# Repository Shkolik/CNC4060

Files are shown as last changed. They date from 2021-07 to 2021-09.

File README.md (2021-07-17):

# DIY CNC router with work area around 400x600mm 

Hi everyone! It's my first attempt to model CNC router in CAD software. Work still in progress, but CAD pretty much done. 

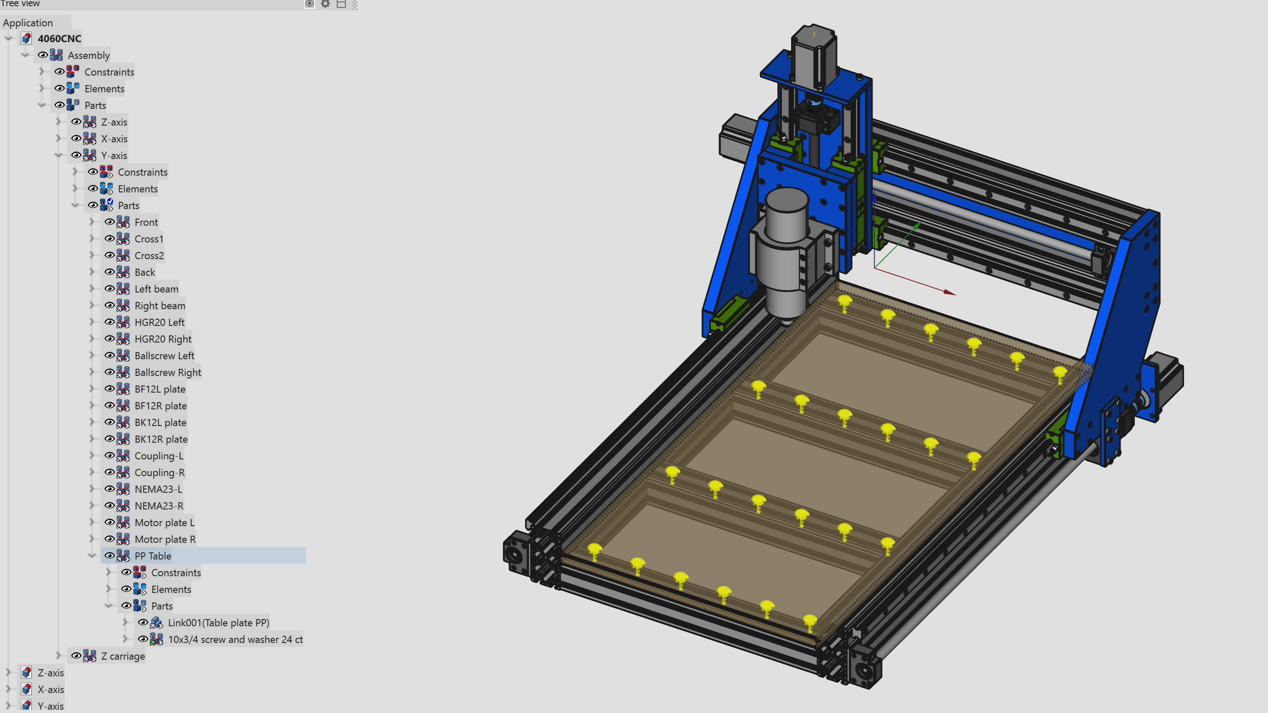
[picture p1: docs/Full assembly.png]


# Materials

Router made of 10 series fractional aluminum extrusion profiles and aluminum flat stock. Base made of 2 2"x4" side profiles and 4 2"x2" cross members. Gantry made of 2 2"x2" profiles that tied together with 1/2" aluminum plate. All sizes and shapes made to fit widely available flat stock.

Fasteners are mix of metric and imperial threads just because all linear motion hardware use metric, but fractional extrusion wants imperial. You can use all metric, but it will require some additional work.

# CAD

Project created in FreeCAD Link. You can find latest releases here: https://github.com/realthunder/FreeCAD_assembly3/releases

Also you need to install Fasteners workbench: https://github.com/shaise/FreeCAD_FastenersWB

To open project without errors and broken links please maintain folders structure as-is.

## Disclaimer

This project provided as-is. You can use it to create you own CNC, but there is no guarantee that it will work as you want and will not produce any loss or injury. 
**Work still in progress!** 

If you have any suggestions - post them as issue inside this repo.

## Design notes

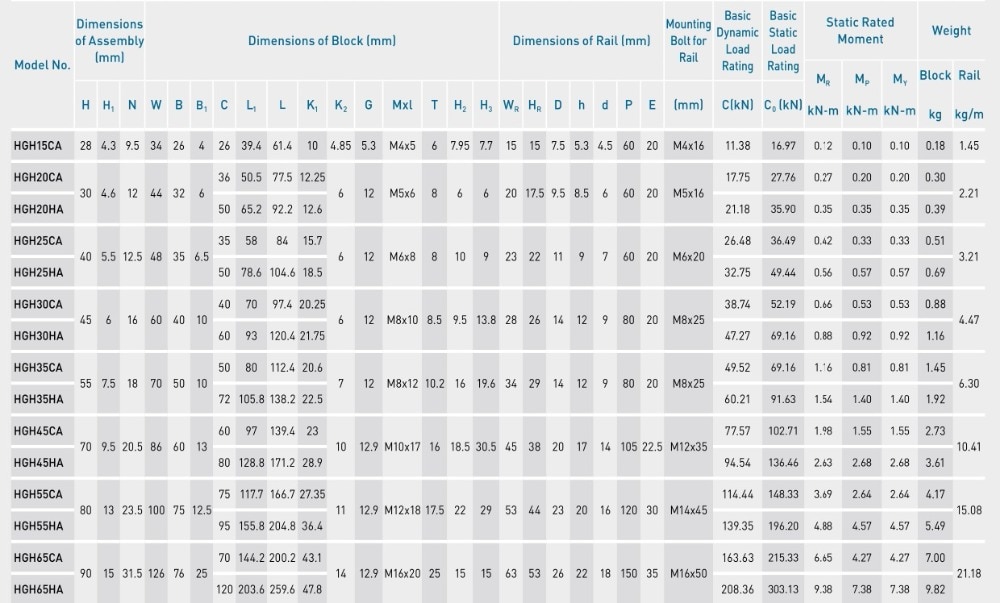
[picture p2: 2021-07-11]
docs/rails.jpg

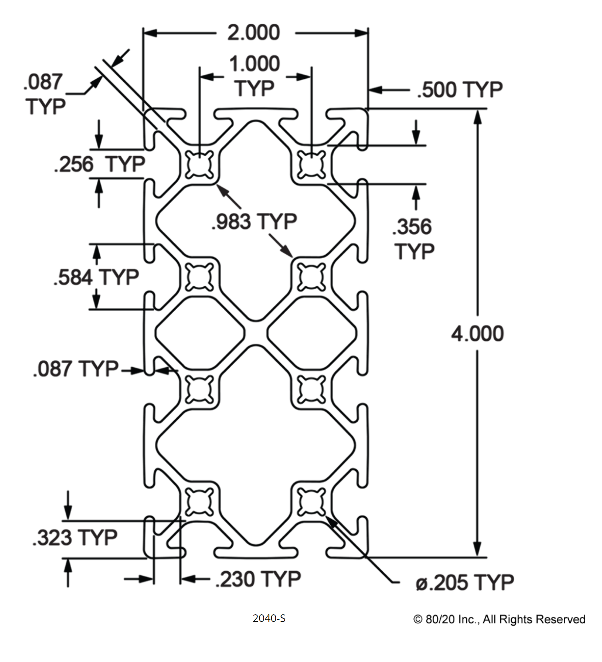
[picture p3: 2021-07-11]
docs/2x4EXT.png

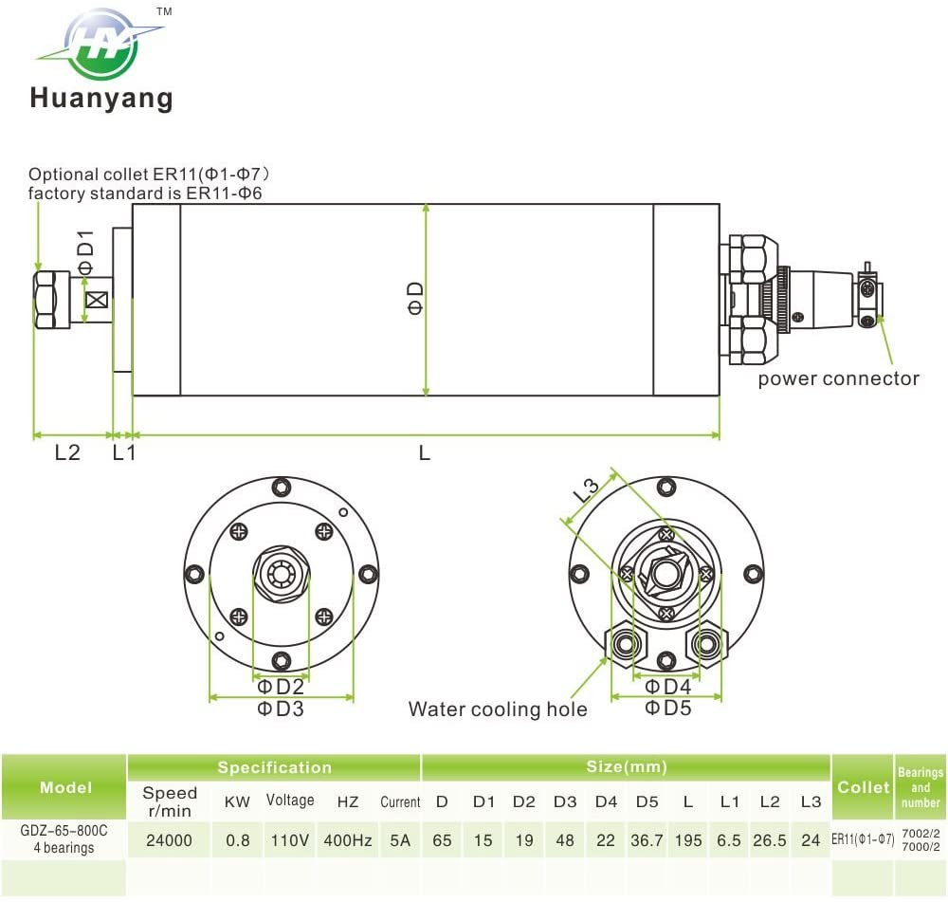
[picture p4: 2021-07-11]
docs/GDZ-65-800C.jpg

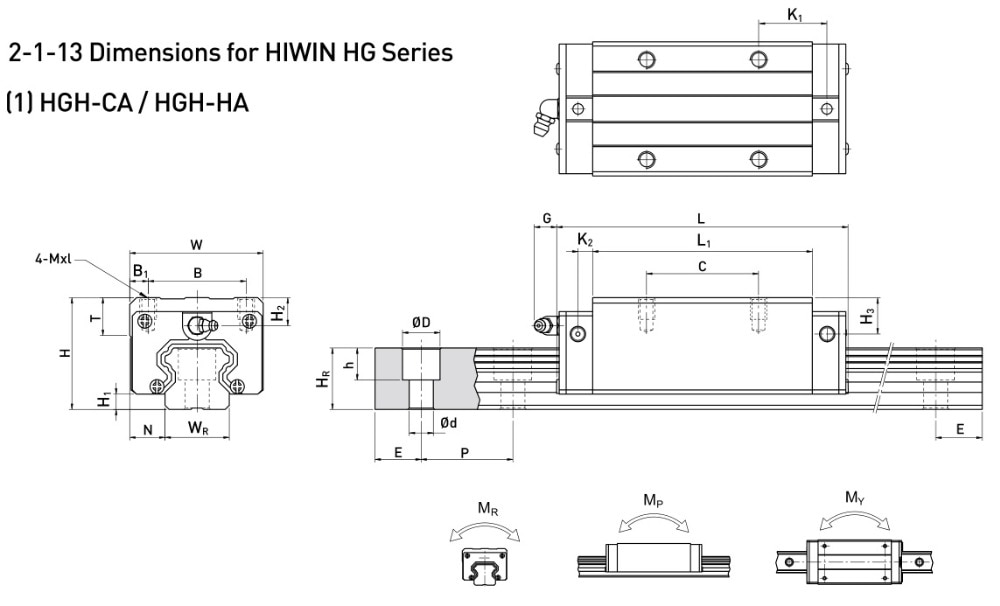
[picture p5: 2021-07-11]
docs/rail_cad.jpg

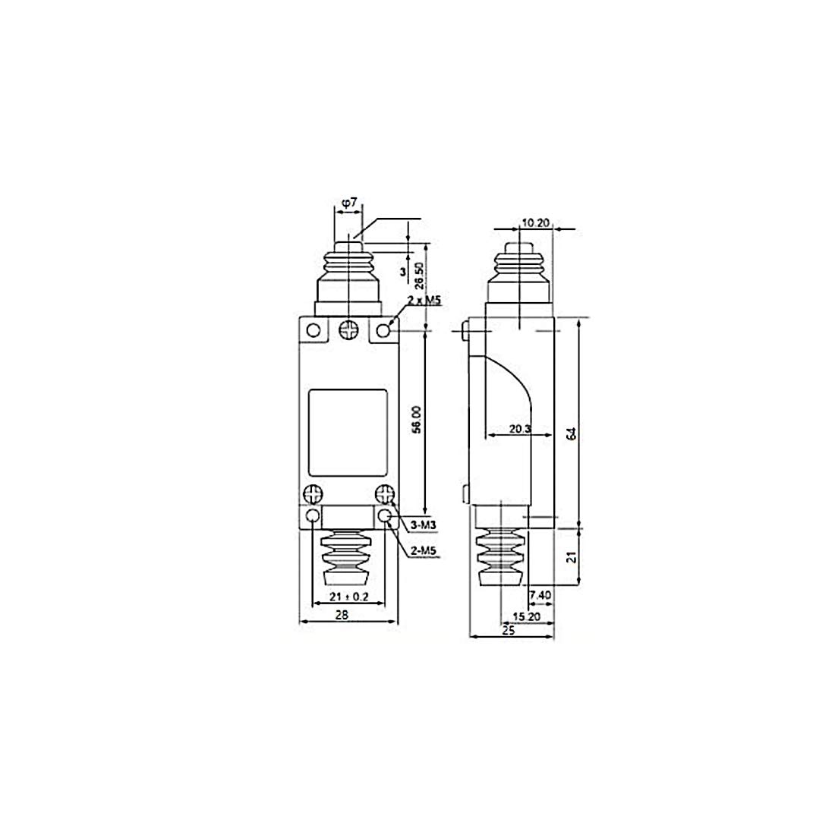
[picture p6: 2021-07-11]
docs/limit_sw_.jpg

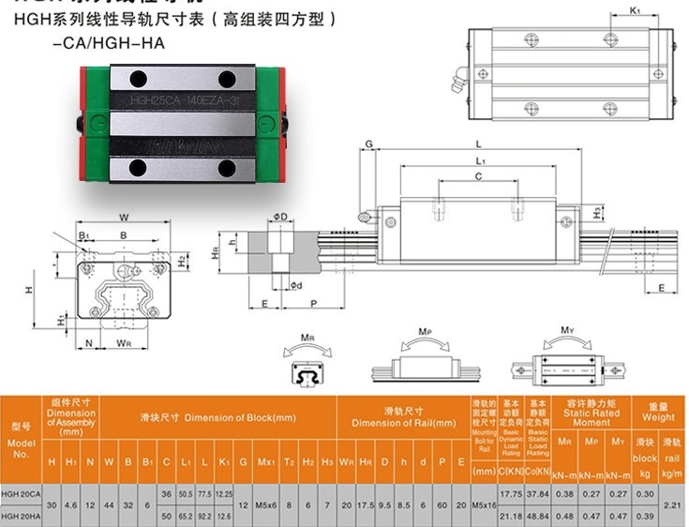
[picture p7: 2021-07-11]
docs/HGH20CA.jpg

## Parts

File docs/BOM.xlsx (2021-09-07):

Item name | price per unit | taxes | 1297.89$ already paid | unit | Link | service price
sfu1605 250mm set | 37 | 2.61 | 39.61 | pcs | https://www.amazon.com/gp/product/B08QHYSK64
4HGR20x800 + 8 HGH20CA + 2sfu1605 800mm | 179.98 | 14.84 | 189.43 | pcs | https://www.amazon.com/gp/product/B08Q38TK1D
sfu1605 550mm set | 36.09 | 2.98 | 39.07 | kit | https://www.amazon.com/gp/product/B07T6FKRBF
HGR20x300mm X 2 + 4xHGH20CA | 45 | 3.71 | 48.71 | pcs | https://www.amazon.com/gp/product/B08BWN8V7P
5/8" X 6" ALUMINUM 6061 FLAT BAR 12" Long | 46.99 | 3.88 | 50.87 |  | https://www.ebay.com/itm/360976433618
Controller PCB | 5.5 |  | 5.5 |  | JLCPCB
Makita RT0701C router | 80 | 6.8 | 86.8 |  | https://www.amazon.com/gp/product/B00E7D3V4S
3/4 aluminum flat 12"x16" | 62.54 | 9.94 | 130.38 |  | https://www.ebay.com/usr/6061dude
1/2 aluminum flat 2 1/2" x 30" | 17.64
1/4 aluminum flat 4"x20" | 9.99
shipping | 30.27
electronics components for BB | 25 |  | 25 |  | https://www.mouser.com
Teensy 4.1 | 30 |  | 30 |  | https://www.mouser.com
Limit switches 4pcs | 14.5 | 1.2 | 15.7 |  | https://www.amazon.com/gp/product/B07V4PR84Y
Stepper drivers 2pcs DM556 | 29.98 | 2.48 | 32.46 |  | https://www.amazon.com/gp/product/B07WRR2HS6
Stepper drivers 2pcs DM556 | 37.98 | 3.13 | 41.11 |  | https://www.amazon.com/gp/product/B082QT6QMZ
router clamp | 25.99 | 2.15 | 28.14 |  | https://www.amazon.com/gp/product/B091K5XS71
Power supply 48V 600W | 40.99 | 3.38 | 44.37 |  | https://www.amazon.com/gp/product/B079D916WY
Steppers Nema 23 269oz-in 2pcs | 51.98 | 4.29 | 56.27 |  | https://www.amazon.com/gp/product/B081MX4PDC
Steppers Nema 23 269oz-in 2pcs | 51.98 | 4.29 | 56.27 |  | https://www.amazon.com/gp/product/B081MX4PDC
Collect reducer | 6.69 | 0.55 | 7.24 |  | https://www.amazon.com/gp/product/B07WNNV1BW
SSR 25A 2pcs | 9.99 | 0.81 | 10.8 |  | https://www.amazon.com/gp/product/B07QJ9KHHZ
Drag chain R38 18mm x 38mm 2pcs | 29.25 | 2.41 | 31.65 |  | https://www.amazon.com/gp/product/B07QZR6BVX
Aviation Connector 16mm 5P | 10.99 | 0.9 | 11.98 |  | https://www.amazon.com/gp/product/B082QPBMDD
Aviation Connector 16mm 3P | 9.99 | 0.82 | 10.81 |  | https://www.amazon.com/gp/product/B082QSVJZM
22awg 4 conductor cable 100ft | 30 | 2.47 | 32.47 |  | https://www.amazon.com/gp/product/B071DFJR8P
10-32 ECONOMY T-NUT | 0.12 | 82 | 9.84 | https://www.tnutz.com/product/et-010-10-32/
#10 WASHER | 0.05 | 24 | 1.2 | https://www.tnutz.com/product/s-a-e-flat-washer/
1/4 WASHER | 0.05 | 40 | 2 | https://www.tnutz.com/product/s-a-e-flat-washer/
M5x12 BH | 0.12 | 8 | 0.96 | https://www.tnutz.com/product/metric-button-head/
M5x16 | 0.12 | 82 | 9.84 | https://www.tnutz.com/product/metric-socket-head/
M5x20 bh | 0.16 | 32 | 5.12 | https://www.tnutz.com/product/metric-button-head/
M5x30 | 0.24 | 20 | 4.8 | https://www.amazon.com/M5-0-8-Socket-Screws-Stainless-Machine/dp/B07KMY7MN8
1/4-20 x 1/2 BH | 0.08 | 8 | 0.64 | https://www.tnutz.com/product/imperial-button-head/
1/4-20 x 1in | 0.13 | 22 | 2.86 | https://www.tnutz.com/product/imperial-socket-head/
1/4-20 x 1in BH | 0.12 | 48 | 5.76 | https://www.tnutz.com/product/imperial-button-head/
1/4-20 x 1 3/4 in BH | 0.25 | 24 | 6 | https://www.tnutz.com/product/imperial-button-head/
10-32 x 3/8in CSH | 0.09 | 12 | 1.08 | https://www.tnutz.com/product/imperial-flat-head/
10-32 x 3/4in BH | 0.12 | 24 | 2.88 | https://www.tnutz.com/product/imperial-button-head/
M5x20 | 0.14 | 30 | 4.2 | https://www.tnutz.com/product/metric-socket-head/
Extrusion:
2"x4" 830mm (~32 11/16 in) | 27.7 | 2 | 55.4 | https://www.tnutz.com/product/ex-2040/?attribute_pa_length-in=32&attribute_pa_fractional-length=0-688-11-16
2"x2" 609.6mm (24 in) | 12.5 | 2 | 25 | https://www.tnutz.com/product/ex-2020/?attribute_pa_length-in=24&attribute_pa_fractional-length=0-000
2"x2" 448mm (~17 11/16 in) | 9 | 4 | 36 | https://www.tnutz.com/product/ex-2020/?attribute_pa_length-in=17&attribute_pa_fractional-length=0-688-11-16
Shipping |  |  | 26.67
Table
Particle board | 21 |  | 21
Brackets | 32 |  | 32
2x4 wood | 20 |  | 20

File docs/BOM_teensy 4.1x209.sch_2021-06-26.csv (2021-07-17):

ID | Name | Designator | Footprint | Quantity | Manufacturer Part | Manufacturer | Supplier | Supplier Part | Price
1 | 100n | C1,C2,C8,C9,C11,C12 | C0805 | 6
2 | 10n | C3,C5,C6,C7 | C0805 | 4
3 | 1nF | C4 | C1210 | 1
4 | 1uF | C10,C13 | C1206 | 2
5 | BAT54SSOT-23 | D1,D2,D3,D4 | SOT-23 | 4
6 | FRAME_B_L | FRAME3,FRAME4 |  | 2
7 | EL357N | IC1,IC2,IC3,IC4,IC5,IC6,IC7,IC8,IC9,IC10 | EL357N-G | 10
8 | 74AHCT541A | IC11,IC12,IC17 | TSSOP20-NXP | 3
9 | 74LVC2G17 | IC13,IC14 | DCK | 2
10 | 24LCxxx | IC15 | SOIC-8(MICROCHIP) | 1
11 | 74LVC1G32DBV | IC16 | DBV-SOT-23 | 1
12 | LM358D | IC18 | SO08 | 1
13 | ULN2003AD | IC19 | SO16 | 1
14 | MAGJACK-RB1-125BAG1A | J1 | MAGJACK-RB1-125BAG1A | 1
15 | PINHD-1X4 | JP1,JP3,JP4,JP6,JP9,JP12,JP13 | 1X04 | 7
16 | PINHD-1X6 | JP5 | 1X06 | 1
17 | PINHD-2X3 | JP7 | 2X03 | 1
18 | PINHD-1X2 | JP8 | 1X02 | 1
19 | PINHD-2X6 | JP10 | 2X06 | 1
20 | PINHD-1X3 | JP11 | 1X03 | 1
21 | JUMPER-SMT_3_NO_NO-SILK | JP100,JP101,JP102,JP103,JP104,JP106,JP108 | SMT-JUMPER_3_NO_NO-SILK | 7
22 | JUMPER-SMT_2_NO_NO-SILK | JP105,JP107 | SMT-JUMPER_2_NO_NO-SILK | 2
23 | JLCPCB_19-217-GHC-YR1S2-3T | LED1,LED2 | CHIPLED_0603 | 2
24 | TEENSY4.1 | M1 | TEENSY4.1 | 1
25 | 680 | R1 | R0805 | 1
26 | 330 | R2,R3,R4,R5,R6,R7,R8,R9,R10,R11 | R0805 | 10
27 | 47K | R12,R14,R15,R19 | R0805 | 4
28 | 1K | R13,R17,R18,R21 | R0805 | 4
29 | 1M | R16 | R0805 | 1
30 | 2.2K | R20,R22,R29 | R0805 | 3
31 | 100K | R23 | R0805 | 1
32 | 10K | R24,R26,R27,R28 | R0805 | 4
33 | 2K | R25 | B64Y | 1
34 | T35-2 | TR1,TR2,TR3,TR4,TR5,TR6,TR7,TR8,TR9,TR10,TR11,TR17,TR18,TR19,TR20,TR21,TR22,TR23,TR25,TR26 | T35-2 | 20
35 | T35-4 | TR12,TR13,TR14,TR15,TR16,TR24 | T35-4 | 6

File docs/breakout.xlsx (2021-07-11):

ID | Name | Designator | Footprint | Quantity | Manufacturer Part | Manufacturer | Supplier | Supplier Part | Price
5 | BAT54SSOT-23 | D1,D2,D3,D4 | SOT-23 | 4 | 0.4
7 | EL357N | IC1,IC2,IC3,IC4,IC5,IC6,IC7,IC8,IC9,IC10 | EL357N-G | 10 | 3.3
8 | 74AHCT541A | IC11,IC12,IC17 | TSSOP20-NXP | 3 | 1.47
9 | 74LVC2G17 | IC13,IC14 | DCK | 2 | 0.86
11 | 74LVC1G32DBV | IC16 | DBV-SOT-23 | 1 | 0.35
12 | LM358D | IC18 | SO08 | 1 | 0.44
13 | ULN2003AD | IC19 | SO16 | 1 | 0.62
24 | TEENSY4.1 | M1 | TEENSY4.1 | 1
34 | T35-2 | TR1,TR2,TR3,TR4,TR5,TR6,TR7,TR8,TR9,TR10,TR11,TR17,TR18,TR19,TR20,TR21,TR22,TR23,TR25,TR26 | T35-2 | 32 | 9.38
 |  |  |  |  | 16.82

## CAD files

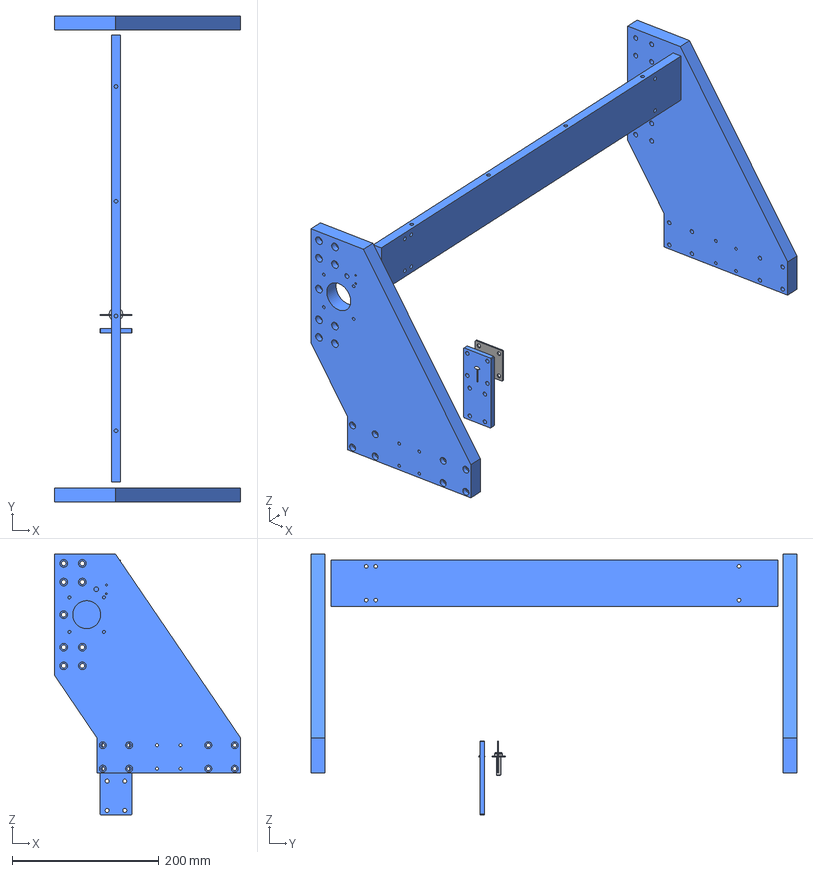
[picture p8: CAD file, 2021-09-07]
cads/parts/X axis plates.FCStd
254.0 x 663.0 x 355.7 mm
Left plate
Right plate
Rear plate
Gouverner shim
Gouverner
1/4in-Nut
1/4inx1in-Screw
M5x20-Screw
M5x12-Screw
M5x20-Screw001
1/4inx1in-Screw001
1/4in-Washer

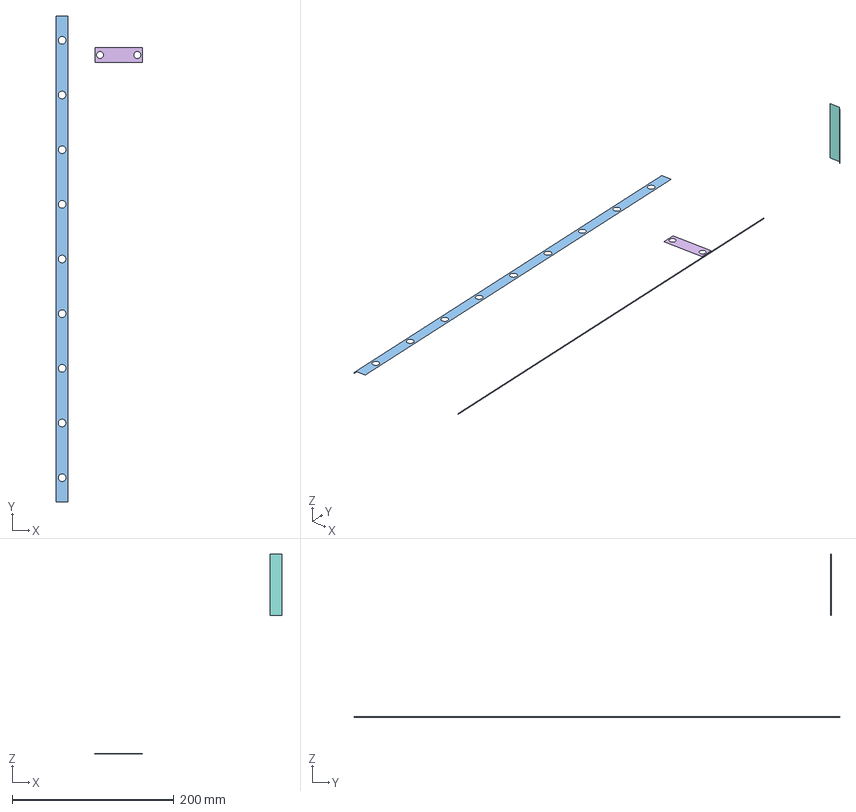
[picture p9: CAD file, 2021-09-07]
cads/X-axis.FCStd
284.0 x 600.0 x 246.9 mm
top-cart-mate
side-cart-mate
top-cart-mate@X-beam Assembly
side-cart-mate@X-beam Assembly
side-cart-mate@X-beam Assembly001
bf-base@Ballscrew-600-Assembly
side-mate@HGH20CA-R-Assembly
top-mate@HGH20CA-R-Assembly

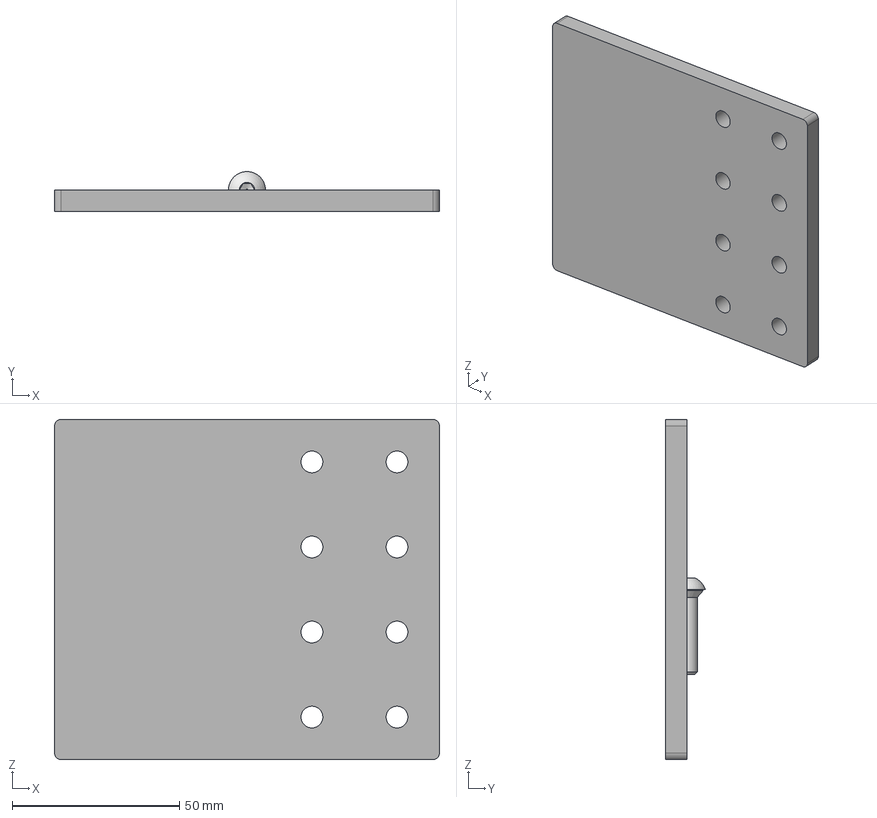
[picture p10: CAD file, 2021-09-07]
cads/parts/Y axis plates.FCStd
115.0 x 11.9 x 101.6 mm
motor plate
front plate
1/4inx1in-Screw
#10x1/2in-Screw
_Element056
_Element057

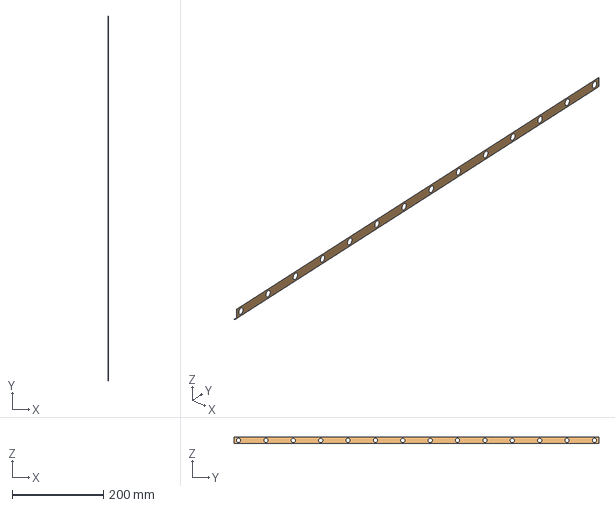
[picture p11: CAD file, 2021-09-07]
cads/Y-axis.FCStd
4.15 x 800.0 x 17.2 mm
side@HGR20-800 Assembly
top-mate@HGR20-800 Assembly

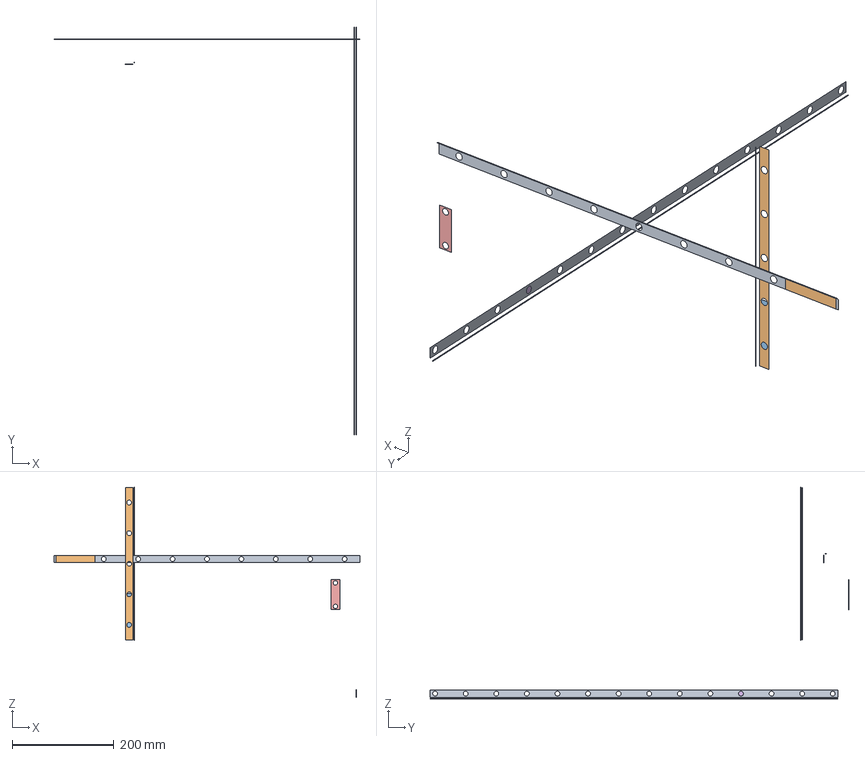
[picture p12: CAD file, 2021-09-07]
cads/4060CNC.FCStd
600.0 x 821.9 x 414.8 mm
top-cart-mate@X-axis Assembly
x-top-rail-top-mate@Z-axis assembly
x-top-rail-side-mate@Z-axis assembly
side-cart-mate@X-axis Assembly
bf-base@X-axis Assembly
top-mate@X-axis Assembly
side-mate@X-axis Assembly
side@Base Assembly
top-mate@Base Assembly
top-mate@Z-axis assembly
top-mate@Z carriage Assembly
r-mate@Z-axis assembly
side-mate@Z carriage Assembly

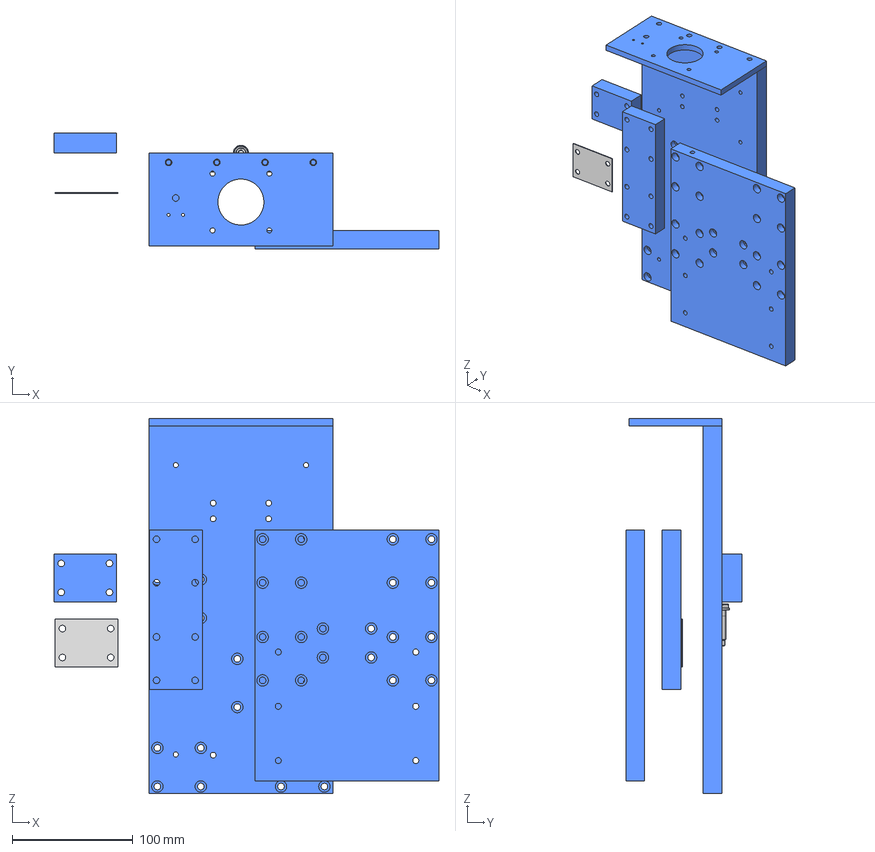
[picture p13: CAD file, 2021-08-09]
cads/parts/Z axis plates.FCStd
319.2 x 96.6 x 311.4 mm
Backplate
Frontplate
Shim
Nut-shim
Motor-bracket
Nut-shim-X
1/4in-Nut
M5x16-Screw
M5x30-Screw
M5x20-Screw
1/4inx1in-Screw
1/4in-Washer

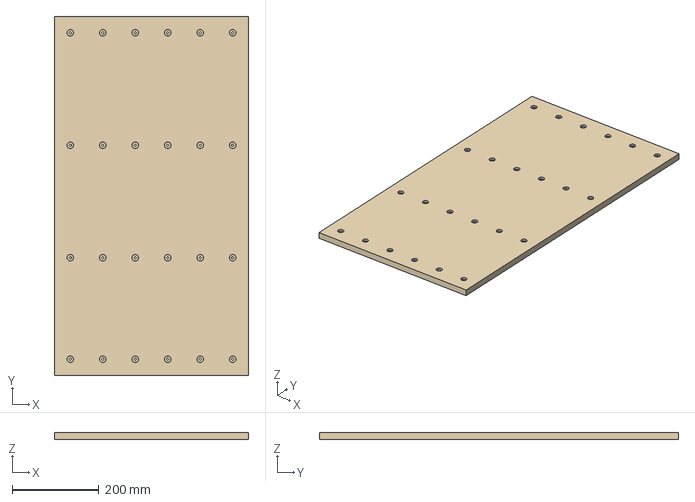
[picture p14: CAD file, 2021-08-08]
cads/parts/Table.FCStd
448.0 x 830.0 x 15.7 mm

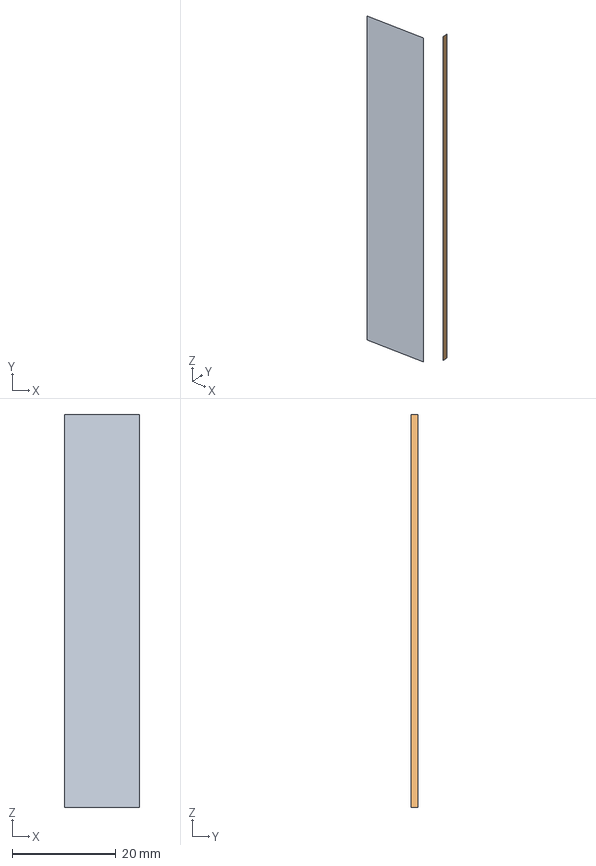
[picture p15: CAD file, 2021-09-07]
cads/Z-carriage.FCStd
17.2 x 4.15 x 75.8 mm
top-mate@HGH20CA-R-Assembly
side-mate@HGH20CA-R-Assembly

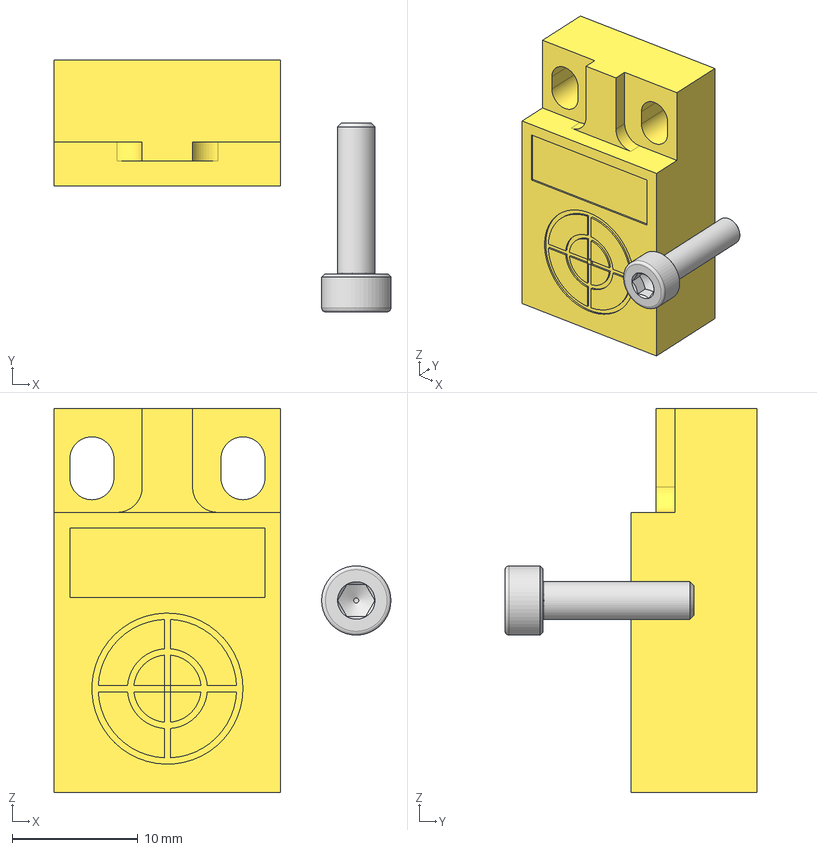
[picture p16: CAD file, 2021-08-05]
cads/parts/LimitSensor.FCStd
26.7 x 20.0 x 30.5 mm
Limit sensor
M3x12-Screw
_Element

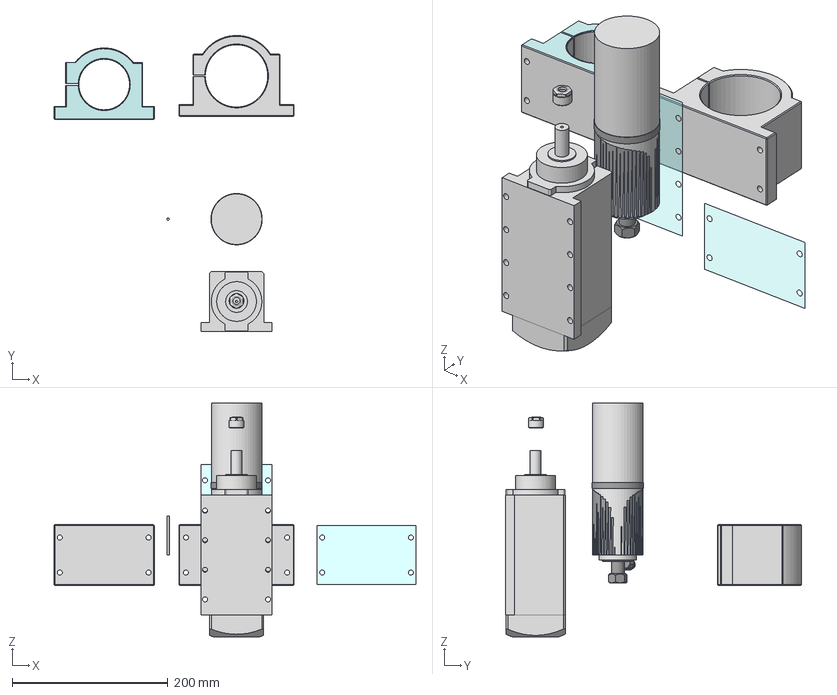
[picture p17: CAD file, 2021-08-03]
cads/parts/Spindle.FCStd
465.0 x 380.2 x 300.0 mm
1.5kw air
ER11
Tool
0.8KW water
65mm bracket
80mm
Makita RT0701C
1/4inx1in-Screw
_Element
_Element001
_Element016
_Element021
_Element022

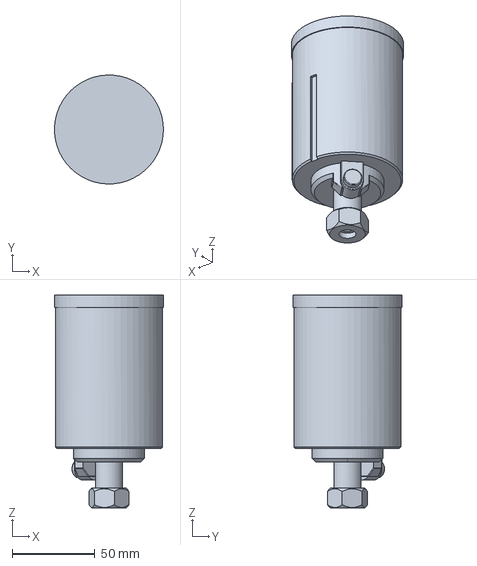
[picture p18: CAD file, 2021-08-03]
cads/parts/Makita RT0701.FCStd
65.9 x 66.0 x 129.0 mm

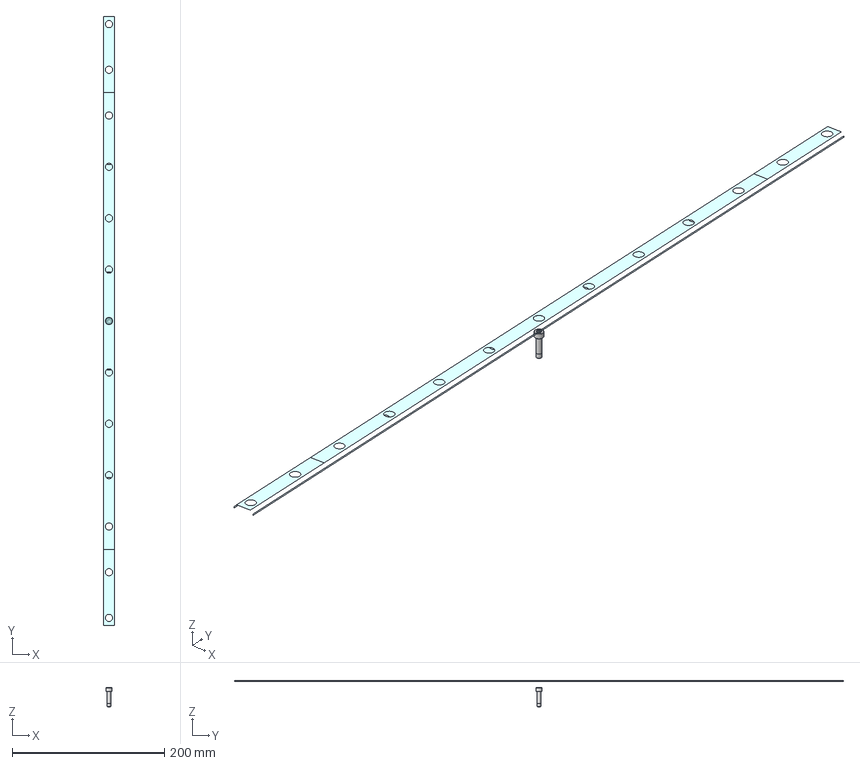
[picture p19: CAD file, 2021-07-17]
cads/parts/HGR20.FCStd
20.0 x 800.0 x 37.5 mm
r-mate
l-mate
top-mate x 3
side-mate
side1
side2
M5x16-Screw
M5x20-Screw

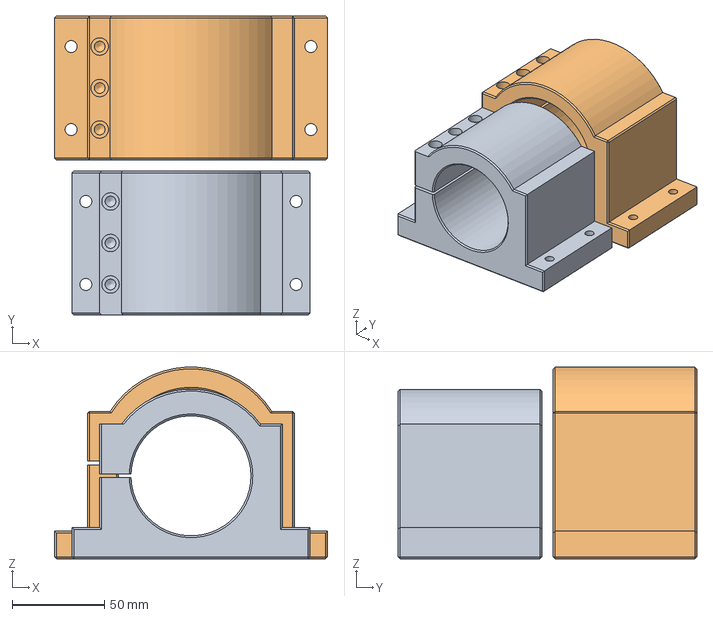
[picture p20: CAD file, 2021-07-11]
cads/parts/SpindleBracket.FCStd
148.0 x 162.0 x 103.9 mm
65mm
80mm

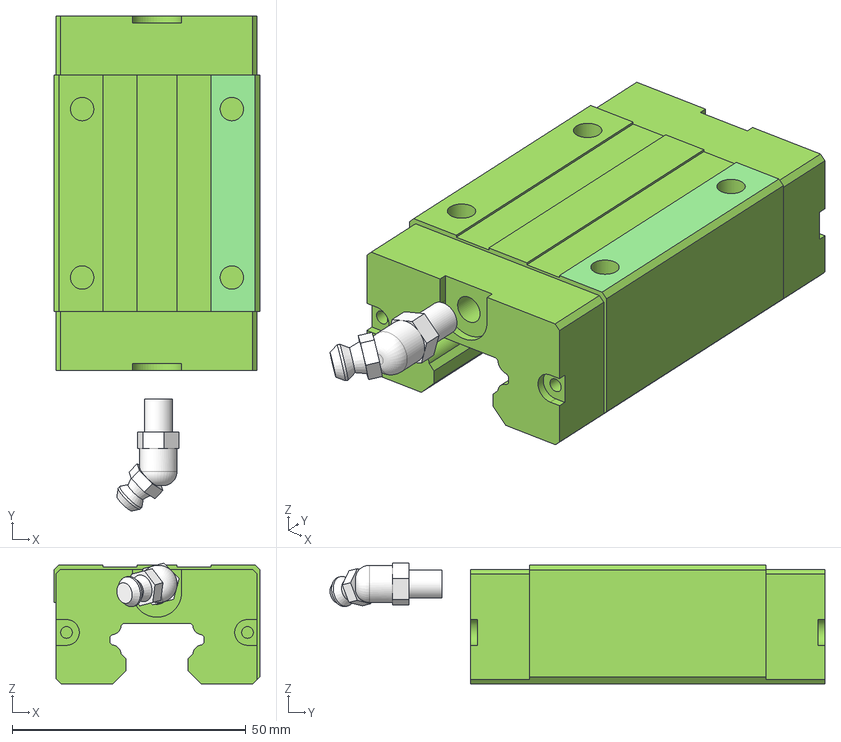
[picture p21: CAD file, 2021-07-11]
cads/parts/HGH20CA.FCStd
44.0 x 105.8 x 25.8 mm
HGH20CA
Greaser
top-mate
side-mate
_Element
_Element005

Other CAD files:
cads/Z-axis.FCStd
cads/parts/BallNut.FCStd
cads/parts/Ballscrew.FCStd

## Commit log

2021-07-11 cads and docs added
    [4060CNC.FCStd, BOM.xlsx, BOM_teensy 4.1x209.sch_2021-06-26.csv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]
2021-07-11 - some links fixed - steel plates thickness changed from 1/8in to 5mm
    [4060CNC.FCStd, Ballscrew.FCStd, X axis plates.FCStd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]
2021-07-12 - Particle plate table added - Side plates layout and thickness changed to make it stiffer and easier to find material - BOM updated
    [4060CNC.FCStd, BOM.xlsx, HGR20.FCStd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]
2021-07-12 - Z axis carriage detached from z-axis assembly. Now all moving constraints in main assembly.
    [4060CNC.FCStd, Z axis plates.FCStd, Z-axis.FCStd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]
2021-07-12 -minor changes in constraints
    [4060CNC.FCStd, X-axis.FCStd, Z axis plates.FCStd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]
2021-07-17 - all fasteners added to assemblies
    [4060CNC.FCStd, BOM_teensy 4.1x209.sch_2021-06-26.csv, BallNut.FCStd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]
2021-07-17 - screenshot added
    [BOM.xlsx]
2021-07-23 - front plates added - Makita RT0701C spindle variant added - Frontplate on z-carriage was adjusted for new spindle variant
    [4060CNC.FCStd, BOM.xlsx, Makita RT0701.FCStd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]
2021-08-03 - Drawings added to Y-axis plates projects
    [4060CNC.FCStd, Y axis plates.FCStd]
2021-08-03 - drawings updated
    [Y axis plates.FCStd]
2021-08-05 - limit sensors added - BOM updated
    [4060CNC.FCStd, BOM.xlsx, LimitSensor.FCStd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]
2021-08-06 - Y axis plates drawings
    [Y axis plates.FCStd]
2021-08-06 z carriage limit bolt
    [Z-carriage.FCStd]
2021-08-06 Y axis plates - complete drawings
    [Y axis plates.FCStd]
2021-08-07 gantry and z-axis drawings
    [X axis plates.FCStd, X-axis.FCStd, Z axis plates.FCStd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]
2021-08-07 few more drawings for z axis parts
    [Z axis plates.FCStd]
2021-08-08 z axis drawings updated
    [4060CNC.FCStd, Table.FCStd, X-axis.FCStd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]
2021-08-09 some drawings fixed
    [X-axis.FCStd, Y-axis.FCStd, Z axis plates.FCStd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]
2021-09-07 - drawings update
    [4060CNC.FCStd, X axis plates.FCStd, X-axis.FCStd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]
2021-09-07 - bom updated
    [BOM.xlsx]
